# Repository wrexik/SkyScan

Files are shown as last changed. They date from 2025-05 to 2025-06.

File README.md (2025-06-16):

# SkyScan
An autopilot 4'' FPV drone with INAV and OpenIPC used for photogrametry!

---

**Say hello to SkyScan!** This is my personal project for [Hackclub Highway](https://highway.hackclub.com/). It will be used to take pictures and videos later to be used for photogrammetry and 3DGS.

 -> Just like this: [3DGS example](https://splatter.app/s/c07-ax0)

## Table of Ideas
- Under 250g
- 4" frame
- Digital FPV with OpenIPC
- INAV - GPS and Mission planning
- 4S battery

## Conectivity
- OpenIPC - 2.4GHz > Realtime HD video
- ELRS - 900MHz > Long range control
- GPS - 1.5GHz > Location & telemetry

## Why did I make this?
As a someone who got absolutlely obsessed with photogrammetry and 3DGS, I wanted to not be limited to taking photos from the bottom of the object or building.
I was told that I just need to get a drone, you know. Get. A. Drone. Then highway email came to me, and I was like, "I can make my own drone, and it will be better than anything you can buy!". OFC! So this is my journey how I learned about all the components, learned how to CAD and how to stay motivated for a longer period of time.

## What is this?
The idea is to create a lightweight drone, that you can just say a location and it will take photos of the object from all angles, and then you can use those photos to create a 3D model of the object.
Like something that DJI has, but with no hardware limitations and open source software!

## Custom 3D Printed Frame
Ive designed a custom frame that could be printed on all 22x22cm printers. So that you could easily replicate it. The frame is designed to be lightweight, but also strong enough to withstand crashes. It supports both 25.5x25.5mm and 30.5x30.5mm mounting patterns for the AIO flight controller and VTX. The files are fully open source and available in the [3d project files](/3d%20parts/3d%20project%20files/) folder.  **Customize it as you want!**
You can print it in any material you want. Or even use CNC machine.

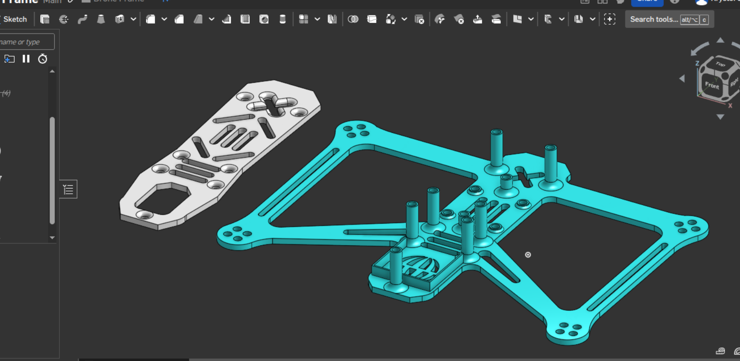
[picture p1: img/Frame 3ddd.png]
Frame

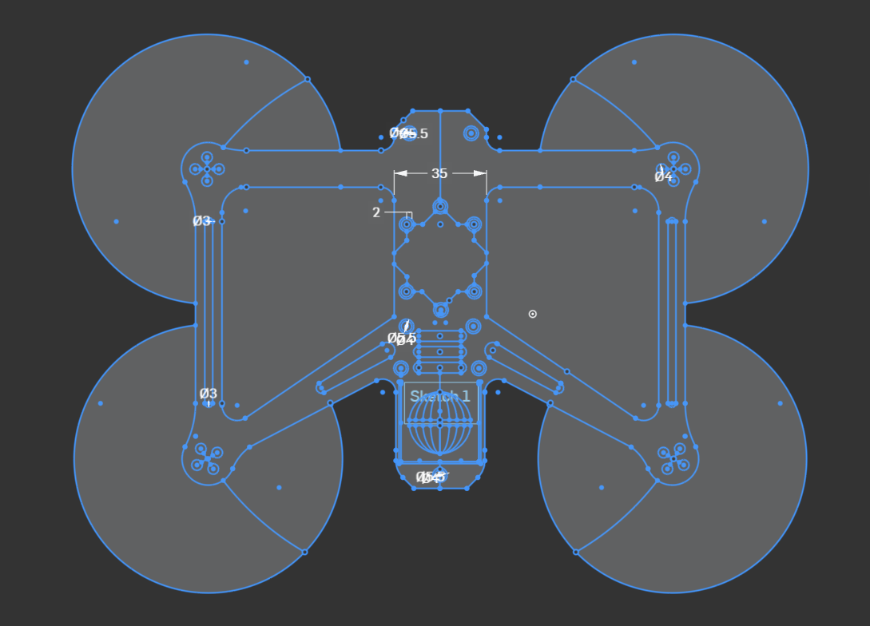
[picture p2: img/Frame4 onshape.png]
Frame drawing

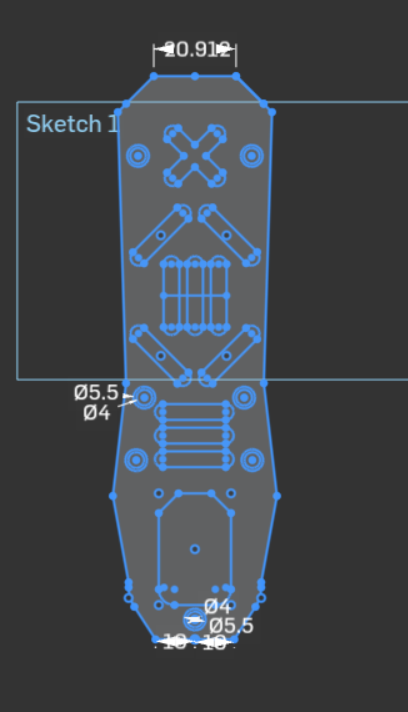
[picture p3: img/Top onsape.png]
Frame shell


``note that the frame does not currently have a camara mount, waiting for the grant to be approved to buy a camera and make it``

# Hardware

  | **Component**                     | **Model / Specs**                                                       | **Notes**                         |
|----------------------------------|--------------------------------------------------------------------------|-----------------------------------|
| **Frame**                        |  Custom 3d printed, my design                                               | supports 25.5x25.5mm, 30.5x30.5mm |
| **Flight Controller + ESC**      | Speedybee F405 AIO 40A (25.5x25.5mm)                                     | BLHeli_32, Bluejay, 3–6S support  |
| **Motors**                       | 4x T-Motor P1604 3800KV                                                  | 4S optimized, 9x9mm mount         |
| **Receiver**                     | Radiomaster XR1 Nano Dual-Band ELRS 2.4GHz + 900MHz                      | High range redundancy             |
| **Radio Controller**             | Radiomaster Pocket (TC-style with built-in ELRS 2.4GHz)                  | No external module required       |
| **Camera & VTX**                 | EMAX Wyvern Link Alpha (OpenIPC support, 5.8GHz HD, 100mW)               | OpenIPC-compatible                |
| **Props**                        | Gemfan Hurricane 4023 / HQProp T4x2.5x3                                  | For 4" efficiency/freestyle       |
| **Battery (light)**              | 4S 850mAh Li-ion                                                         | Sub-250g compatible               |
| **Battery (long range)**         | 4S 18650 3000mAh Li-ion (e.g., VTC6 pack)                                | Up to 40+ min flight              |

This is the camera that makes this all possible. It is a 5.8GHz digital FPV camera with OpenIPC support, which allows you to stream HD video in real-time.
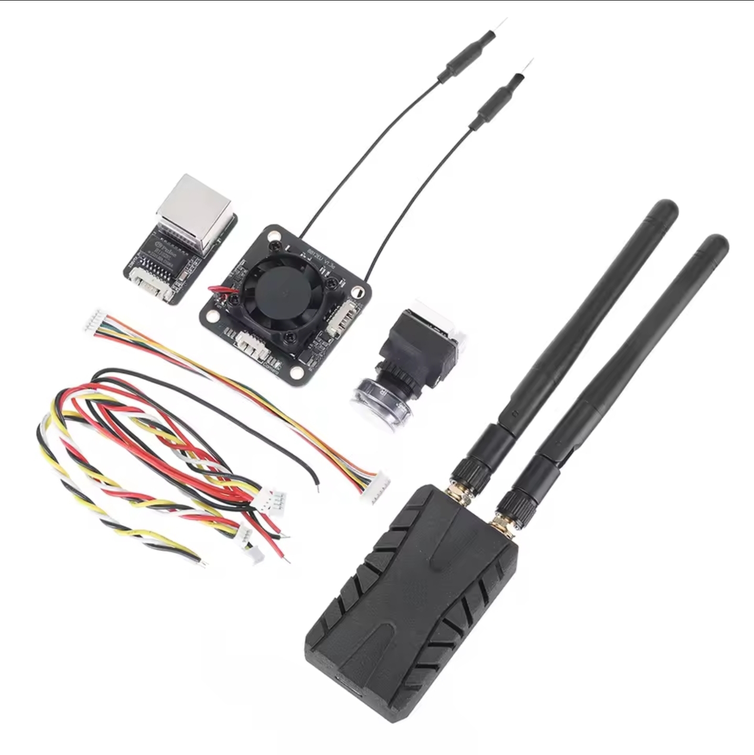
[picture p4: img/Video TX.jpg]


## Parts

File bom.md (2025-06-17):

| **Component** | **Model / Specs** | **Notes** | **Price (CZK)** | **Price (USD)** | **Link** |
|---|---|---|---|---|---|
| Frame | Custom 3d printed, my design (Cost is material spool petg-cf) | supports 25.5x25.5mm, 30.5x30.5mm | 500 | 24 | |
| Flight Controller + ESC | Speedybee F405 AIO 40A (25.5x25.5mm) | BLHeli_32, Bluejay, 3–6S support | 1330 | 61 | [AliExpress](https://a.aliexpress.com/_Ez89AS2) |
| Motors | 4x T-Motor P1604 3800KV | 4S optimized, 9x9mm mount | 1142 | 52 | [AliExpress](https://a.aliexpress.com/_EINYVGa) |
| Receiver | Radiomaster XR1 Nano Dual-Band ELRS 2.4GHz + 900MHz | High range redundancy | 335 | 15 | [AliExpress](https://a.aliexpress.com/_ExRInKe) |
| Camera & VTX | EMAX Wyvern Link Alpha (OpenIPC support, 5.8GHz HD, 100mW) | OpenIPC-compatible | 2350 | 107 | [AliExpress](https://a.aliexpress.com/_EHbSKhC) |
| Props | Gemfan Hurricane 4023 / HQProp T4x2.5x3 | For 4" efficiency/freestyle | 130 | 6 | [AliExpress](https://a.aliexpress.com/_EzHnXNG) |
| Battery (light) | CNHL 4S 850mAh XT30 2pcs | Sub-250g compatible | 820 | 38 | [AliExpress](https://www.aliexpress.com/item/32848174970.html) |
| GPS | Generic M8Q or BN-220 GPS Module | For navigation and failsafe | 600 | 27 | [AliExpress](https://a.aliexpress.com/_ExEMGLG) |
| Buzzer | Standard 5V buzzer with beacon function | Optional but useful | 45 | 2 | [AliExpress](https://a.aliexpress.com/_EHUrHM6) |
| VTX Antenna | U.FL 5.8GHz Antenna | Compatible with Wyvern VTX | 300 | 14 | [AliExpress](https://a.aliexpress.com/_Ev1Kqw6) |
| **Total** | | | **7282** | **329.15** | |

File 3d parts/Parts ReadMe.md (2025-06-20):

The Final 3D parts are:

[Top Shell](/3d%20parts/Top%20Shell.stl)

[Bottom Frame](/3d%20parts/Bottom%20Frame.stl)

The DWG is located in the *3d project files* folder.

And here is the link for OnShape: [Link](https://cad.onshape.com/documents/29a5ea5b7ab0b002b2ab2d66/w/dfc60f1223006b31794c7fb2/e/e7f5c2a8a30eddbf3b560972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)

Some basic measurements
- All Holes are 1.5mm
- 30.5 x 30.5mm and 25.5 x 25.5 mounting frames
- Space for 19 x 19mm GPS module in the back
- Properels are 102.1mm (4 inch)

| Component | Mounting | Diameter | Notes |
| --- | --- | ----- | --- |
| FC AIO | 25.5 x 25.5mm | 1.5mm | 4 x holes |
| VTX | 30.5 x 30.5mm | unknown | 4 x holes|
| Camera | 2 screws from the sides | n/a | 2 x holes, 19 x 19mm body |
| Motors | 9 x 9 mm | M2 / 1.5mm | 4 x holes |

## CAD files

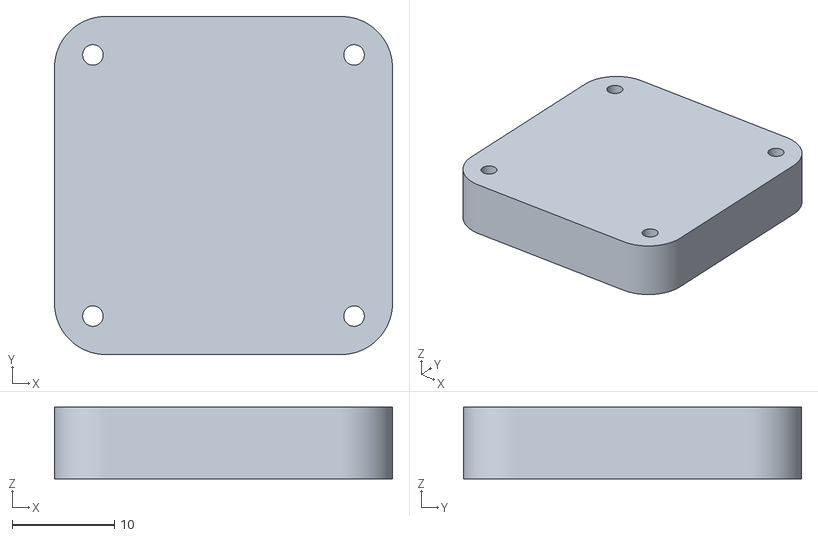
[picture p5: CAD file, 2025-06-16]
3d parts/FC Model.stl
33.0 x 33.0 x 7.00

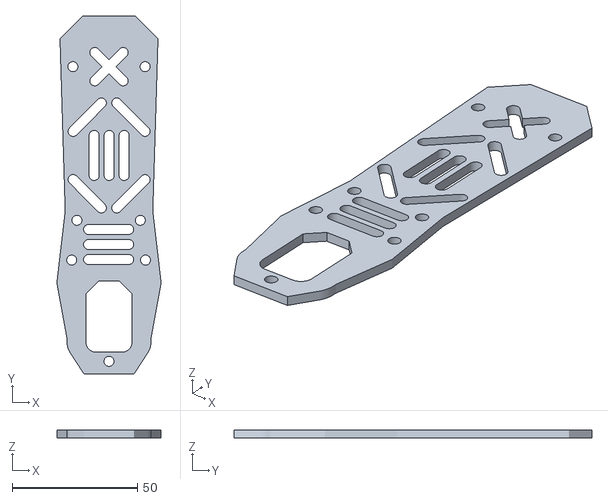
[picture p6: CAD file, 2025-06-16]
3d parts/Top Shell Sharp.stl
41.7 x 143.1 x 3.00

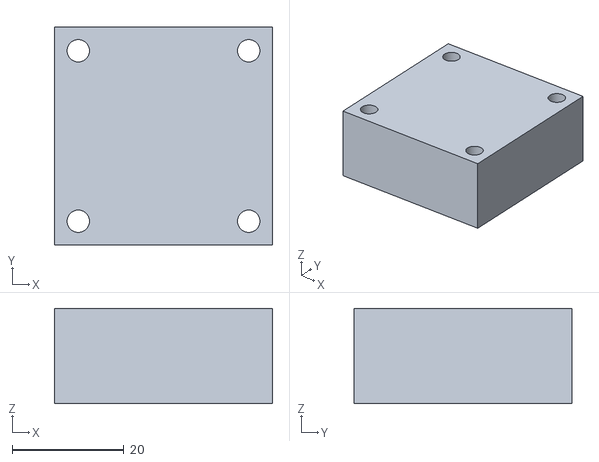
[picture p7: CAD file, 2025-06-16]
3d parts/VTX with fan model.stl
39.0 x 39.0 x 17.0

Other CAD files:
3d parts/3d project files/Drone DWG.dwg

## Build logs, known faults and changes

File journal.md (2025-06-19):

---
title: "SkyScan"
author: "Wrexik"
description: "An autopilot 4'' FPV drone with INAV and OpenIPC used for photogrammetry!"
created_at: "2025-05-21"
time_spent: "6-7h"
---

# 05-21: Initial Repository Creation & Ideas
``Aprox. 2,5 hours of research``

Created a new repository for the SkyScan project.  
I've watched videos on drone building and the INAV firmware.
- Looked into ELRS and OpenIPC for long-range control and video streaming.

Wrote down the following features I would like to accomplish:
- Under 250g due to regulations
- 4" frame
- Digital FPV with OpenIPC
- 4S battery
- GPS and Mission planning with INAV

- Looked into compatibility of OpenIPC and ELRS frequencies. Both are 2.4GHz. So I will need to use a 900MHz ELRS module to make sure that the 2.4GHz and 900MHz modules are not **interfering with each other**.
- Looked up options for the OpenIPC system. Decided to go with **Wyvern Link (Alpha) OpenIPC - 100mW VTX** for its price and good camera.

Aliexpress will be the shop I will be sourcing from — cheap shipping and a huge selection of parts. I have only good experience with Aliexpress. So there isn't another option.

Okay, a few hours later and I have actually a better option for the camera. I will be using the **Eachine Sphere Link 5.8GHz WIFI Digital HD**. Since the Wyvern Link does not support onboard recording, this will be a much better option. And I will be able to use the **5.8GHz** frequency for the video and 2.4GHz for the ELRS.

> this is the Eachine Sphere VTX  
Eachine Sphere VTX

- This was about 2.5 hours of research. I will be continuing to look into the components and their compatibility.

# 05-21: Frame, FC, Motors

I prioritized selecting the camera first because that's the main part of the drone for the actual 3D scanning.

I've continued to look up parts and I think I have a quite good combination now. I'm especially happy with the frame. It's built so the props don’t show in the camera feed. **Clear video is important!**

### As of now, I have selected the following components:

| Component | Details / Notes |
| --- | --- |
| **Frame** | **JMT LR4 169mm (4")** — supports 20x20 / 25.5x25.5mm stacks |
| **Flight Controller + ESC** | **SpeedyBee F405 AIO 40A** — powerful, 25.5x25.5mm mount (fits with adapter or printed plate) |
| **Motors** | **T-Motor P1604 3800KV** — perfect for 4S & 4" props; great efficiency for cruising |
| **Camera/VTX** | **Eachine Sphere Link** — 1080p onboard DVR, MAVLink, 800mW digital FPV |
| **Receiver** | **Radiomaster XR1 Nano ELRS** 2.4GHz/900MHz dual-band — fully INAV + ELRS compatible |

> The frame I've chosen to go with  
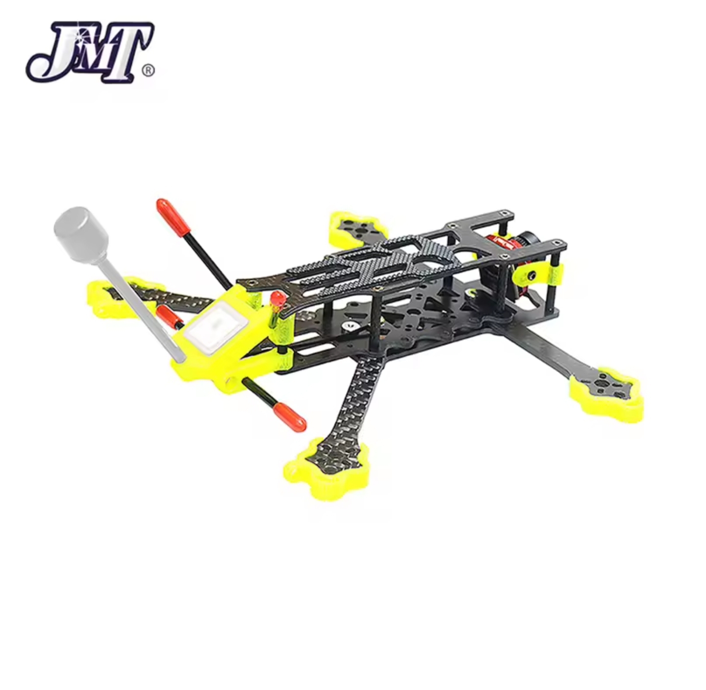
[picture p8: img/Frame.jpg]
Drone Frame


Next steps:
- Look into the GPS recommended by the frame manufacturer, since it already has a GPS mount.
- Learn more about props and their compatibility with the motors.
- Finish with battery selection. **And establish a weight budget.**

My plan for the custom parts are legs that I will model and 3D print. I will also be using a 3D printed mount for the camera. As for custom hardware, the FC has an I2C port; I could use that for a LIDAR or RGB.

That's all for now. Will be back soon!

# 05-22: Component Selection & Weight Budget

`2 hours to school well spent :P`

Hey again, today I started working right after I got into my train. I've decided on a GPS module that will be needed for the drone to have a good position hold while taking pictures.  
The GPS should also have a magnetometer so the drone knows its direction — which the **Beitian BN-880 BN880** has.

Last night I watched a few videos and all of the featured drones had a buzzer. So I figured I might also add one, the FC supports it.

| Component  | Details / Notes |
| --- | --- |
| **GPS** | **Beitian BN-880 BN880 Flight Controller GPS** — Fast and accurate, has magnetometer |
| **Buzzer** | **Pixhawk PX4 Buzzer** — really compact |
| **Props**  | **Gemfan 4023 1.5mm 2mm 4inch 3 blade** — Good looking and in the right size. They should be made for the brand of our motors |

Now I'm looking into props. They should have a 1.5mm hole and 3 blades — 4 inch size of course.  
From what I understand the **4023** are suitable. I've chosen a **pack of 16** since they are quite fragile.

I really like this process of looking up parts and matching them with each other. It’s like building computers — but it FLIES!

With the props added it looks quite complete, just checking a few things with the seller of the drone frame so I could be sure with the dimensions. I CANT WAIT!

I will be sourcing my own batteries & controller. The software part is also what I’m looking forward to — I found some that I could modify for my 3D scanning implementation!

I will have my friend run over the parts and check some of the fitment. The VTX will have to have a custom 3D printed adapter because it’s 0.5mm off. That's no problem — I will practice my patience and CAD skills.

Also an interesting thing I found while researching RX modules and interfering frequencies — the current **Radiomaster XR1 Nano ELRS** is dual-band. So it supports both 2.4GHz and 900MHz. That means I could upgrade for longer range down the road!

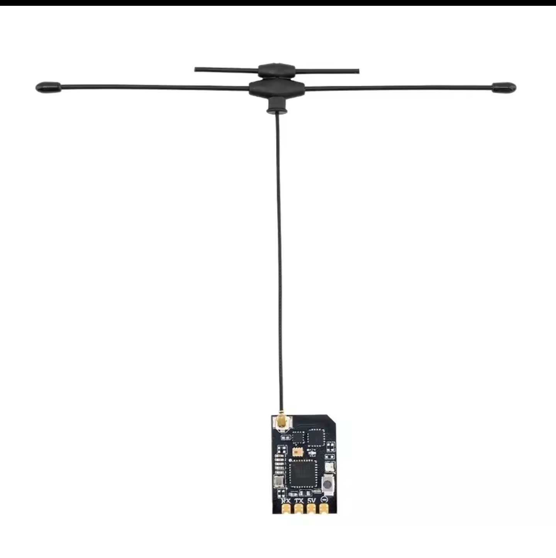
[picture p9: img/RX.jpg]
ELRS RX


Hey I'm back, 2 classes later, I've found this cute pair of lollipop antennas. They will be great for the VTX. Since the drone will be operated remotely on a monitor I would really like a good video feed. Might implement computer vision for object detection.

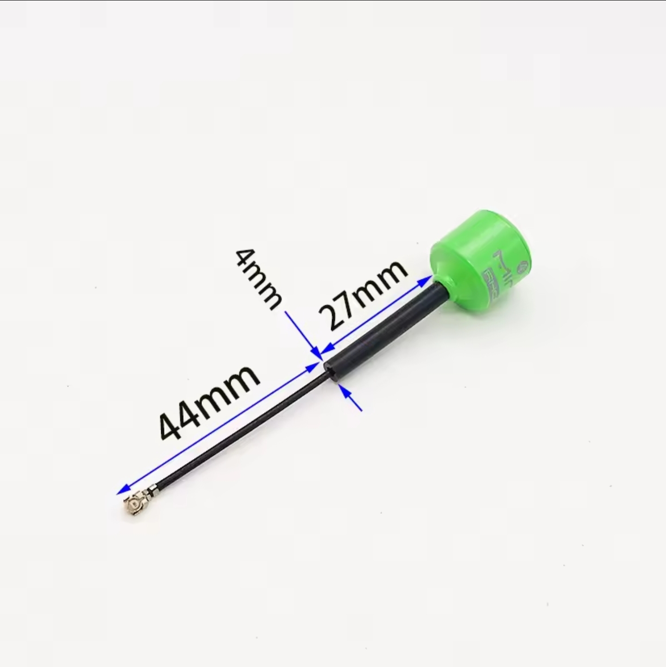
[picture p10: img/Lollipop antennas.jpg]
Antennas


# 05-22/23: Final costs

`took more or less about 30 minutes`

| Parts | Link |  Costs  + Shipping  |
| --- | --- | :---: |
| Frame | https://a.aliexpress.com/_EvwVZDU | 730 CZK - 33.15 USD |
| VTX | https://a.aliexpress.com/_EHbSKhC | 2350 CZK - 107 USD  |
| Motors | https://a.aliexpress.com/_EINYVGa | 1142 CZK - 52 USD |
| VTX Antenna | https://a.aliexpress.com/_Ev1Kqw6 |  300 CZK - 14 USD |
| FC AIO | https://a.aliexpress.com/_Ez89AS2 | 1330 CZK - 61 USD |
| Buzzer | https://a.aliexpress.com/_EHUrHM6 | 45 CZK - 2 USD |
| Props | https://a.aliexpress.com/_EzHnXNG |  130 CZK - 6 USD |
| GPS | https://a.aliexpress.com/_ExEMGLG |  600 CZK - 27 USD |
| RX | https://a.aliexpress.com/_ExRInKe |  335 CZK - 15 USD |
|TOTAL||317.15 USD|

The software side will be so much fun. Im looking forward to it.

---

# 06-11: Custom Frame Modeling for 3D Printing
`2 hours of 3D modeling`

Hey, it's Wrexik again!
Since highway is about making custom parts, so it would make sense to model the frame in 3D. To get the project **approved**! Today I will gather all the measurements and dimensions of the components for the build. I will also be looking for a good 3D material to print the frame with. So far I have been more towards PETG but ABS is also a good option. 
PETG with carbon fiber would be pretty cool. But I dont know if my printer is compatible with it. I will have to check that out.

Ok, now the measurements. I will check out the camera, VTX, FC, motors and GPS.
| Component | Mounting | Diameter | Notes |
| --- | --- | ----- | --- |
| FC AIO | 25.5 x 25.5mm | 2mm | 4 x holes |
| VTX | 30.5 x 30.5mm | unknown | 4 x holes|
| Camera | 2 screws from the sides | n/a | 2 x holes, 19 x 19mm body |
| Motors | 9 x 9 mm | M2 / 2mm | 4 x holes |

Next up, making some kind of footprint for the components. To better understand the way they will fit together.
Decided to try Onshape, ive been using Plasticity for a while but I want to try something new.

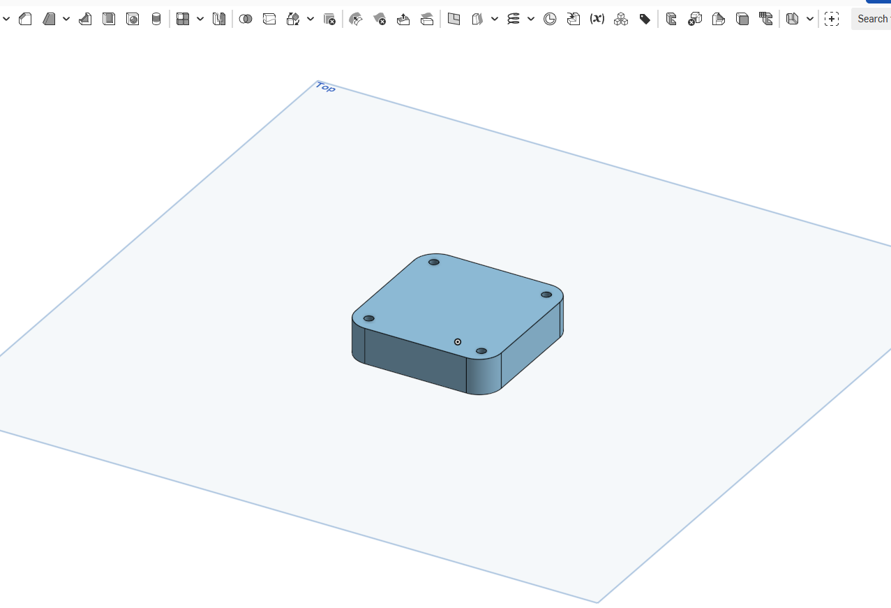
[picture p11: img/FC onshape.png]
Onshape FC model


Its really diferent. I have modeled the Motor and FC so far.
Now im going to model the VTC and GPS.
Here we go then... Did the GPS it will only serve as a reference for the mount. I might skip the GPS mount for now, since I will be using a 3D printed one anyway.
Onto the VTX, Echine doesnt have a good description of the dimensions, so again it will be only a refrence for the frame mounting.

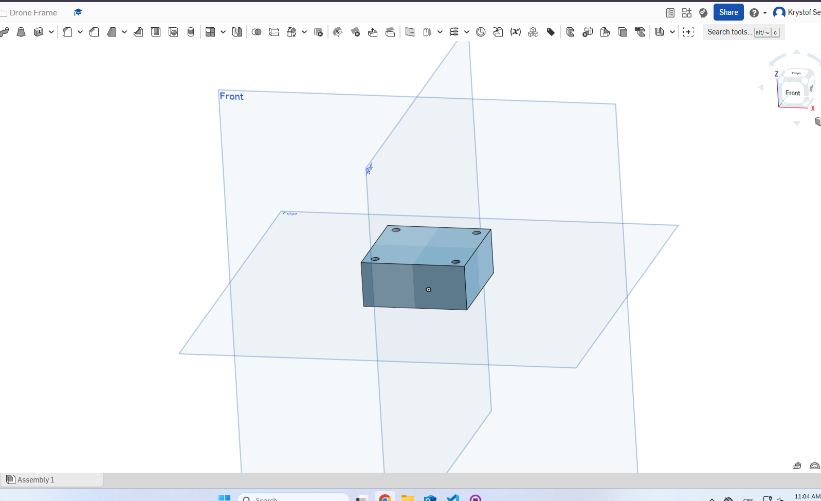
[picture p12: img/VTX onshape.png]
Onshape VTX model


They dont say if the hole is M2 or M3 so I did them as M2. I will have to check that out later. Or just add silicone feet to match the size.

Now the bigger part, the frame itself. I will choose the selected frame as a refrence, and modify it to my liking. It will be pretty basic, but I will be able to modifiy it later on and update it.
The plan is to have "Deadcat" shaped arms, for clean video without the props in the frame. And really lightweight. I have 10 minutes left of the current class, so I will get things togeter and see how it goes.

Anddd End. I've only managed to experiment with the frame. And get the initial idea.

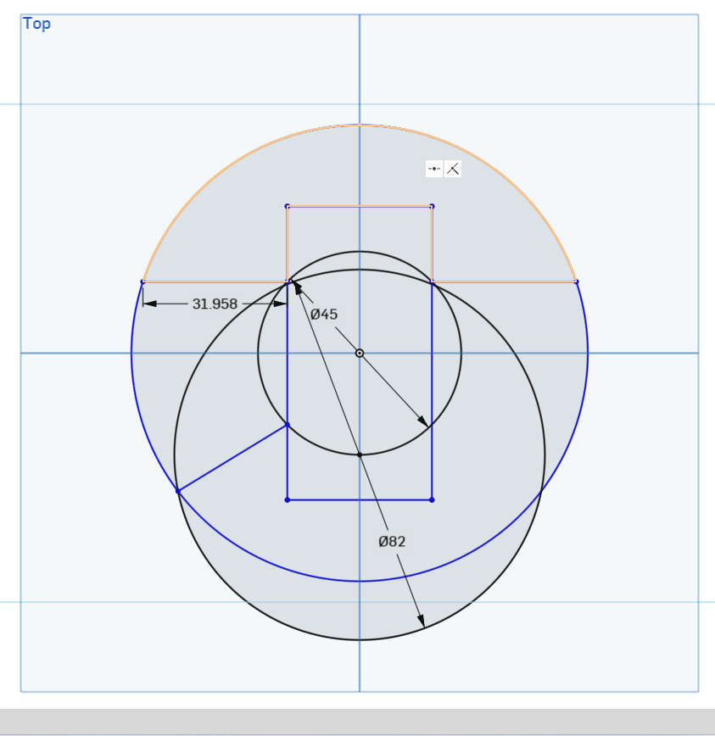
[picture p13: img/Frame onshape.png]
Onshape Frame model


# 06-12: More 3D Design & Frame Modeling
``1,5 hours of 3D modeling``

Ive added the propereller dimensions to make it easier to understand the layout. Ive also made the body little bit longer to fit everything in. It will also help with the center of gravity. I have to shower and go to bed, so I will continue tomorrow. But I think it looks super cool, with the rounded edges. *YEPEE*

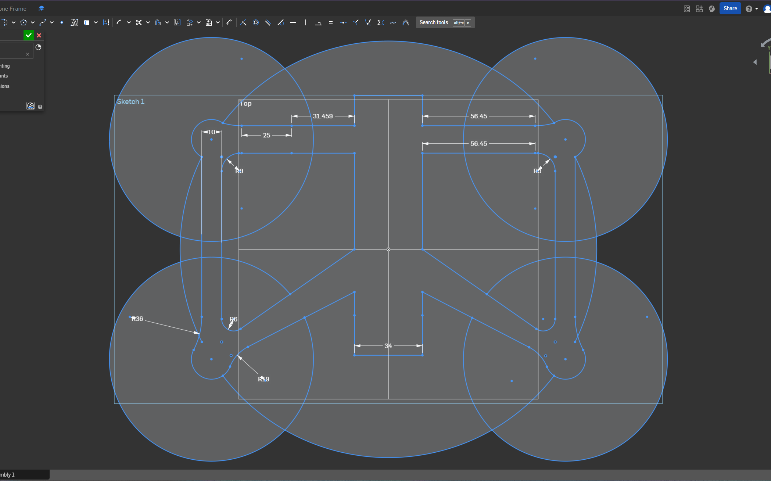
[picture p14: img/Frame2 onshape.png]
Onshape Frame model 2


tomorrow I will try to excrude the frame and try to print the very first prototype. Just to see the sizes and the fitment of the components. Im looking forward to it!

# 06-14: First Prototype Printed
Today I fixed some of the errors in the frame structure. The arms werent the same, I might use mirror mode next time. Ive also rounded more of the frame, it looks super cool now! When I came home from school I extruded the frame by 3mm and tryed to print it. It came in about 28g and 34m of print time. Just in PLA nothing fancy.
Next up, I will be adding the mounting holes and standofs. And the "roof" of the drone.

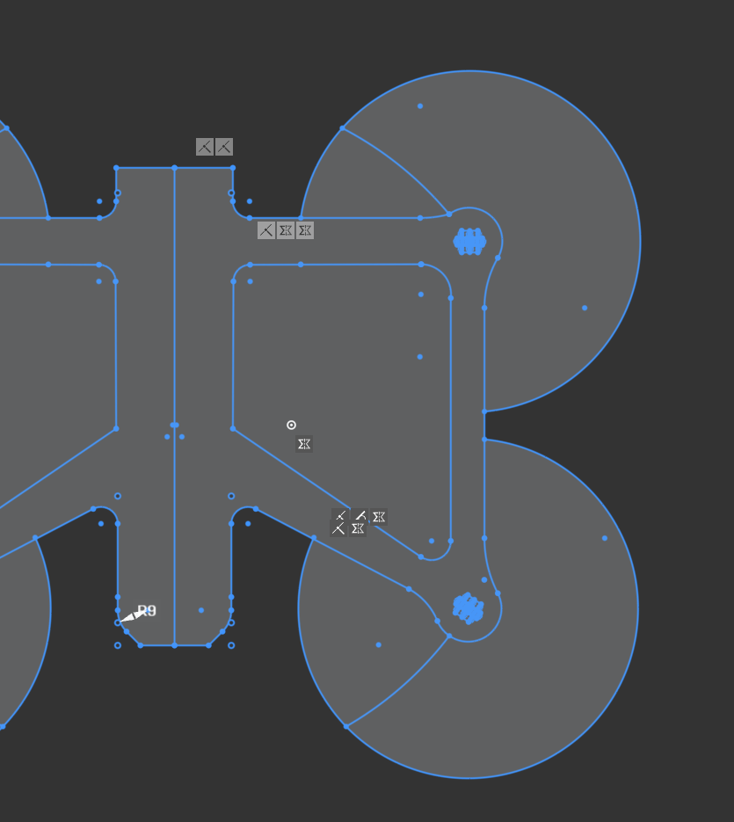
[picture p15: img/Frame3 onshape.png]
Onshape Frame model 3


Ive added the mounting holes for motors and made the back of the drone longer to easily fit the gps and stuff. I will be experementing with the mounting for the motors, Ive made them ajustable. But also left the M2 holes for the non ajustable version. The prototype is printed, older version but it looks sick!

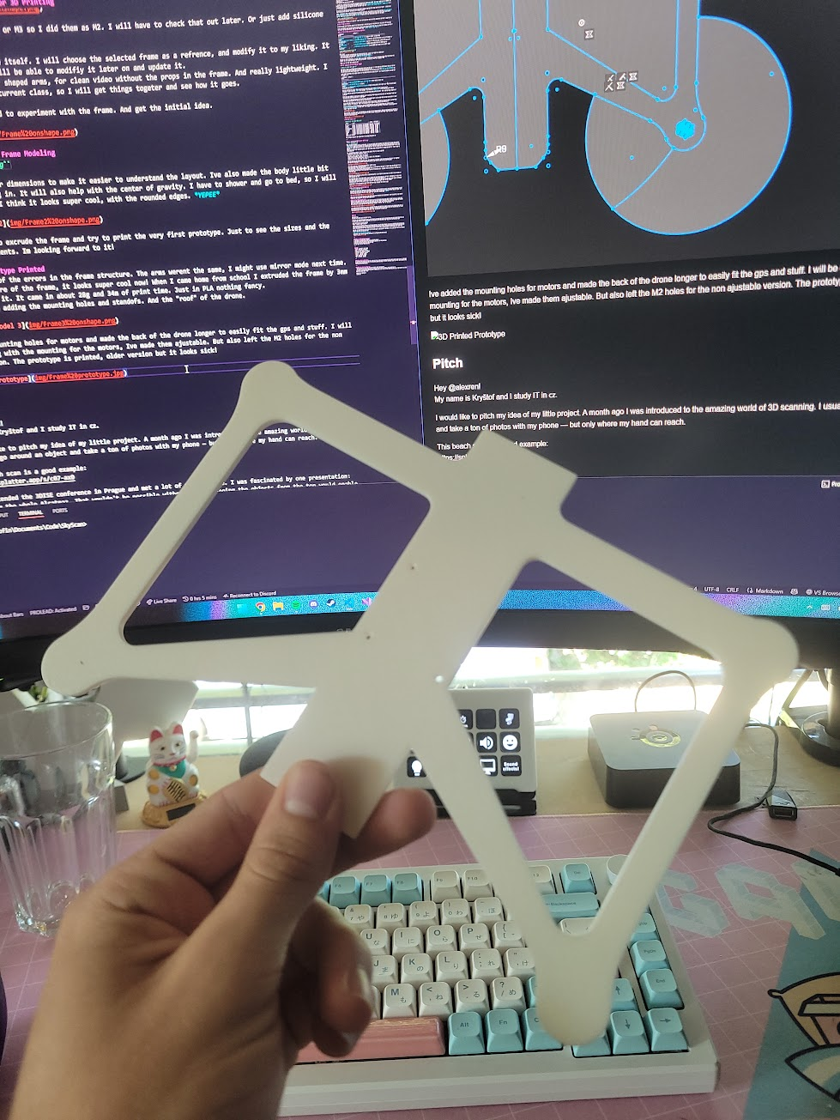
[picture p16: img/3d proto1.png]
3D Printed Prototype


Sorry fot the image quality, my S24 Ultra broke :/.

# 06-16 More CAD! Weight reduction.

``Took some time, 3,5 of CAD and stuff``

Hey, Ive been contimuing to model the frame. Ive looked up frame models and made it how I think it could work. I had the screw dimensions wrong, should be fixed now. I still dont know the diameter of the screw hole on the VTX. In case thats wrong it could be easily fixed after I get the parts from the grant. Ive added holes for mounting the roof of the drone. It will be pretty much the same thing like on the bottom, but with more holes and grill for the VTX fan. Well he might be covered by the battery, but it should work even without it. As far as my motivation goes, Im "motimaxxed" Im doing my best with the documentation for yall. I will work on the ReadMe next. With pretty screenshots. Really praying for approval rn.
Here is the current status of the drone. I had a while to work on it in class.

Onshape Frame model 4

I also looked up some filaments and compared PET-G CF with other options. And again again more holes! Starting with the top now, I need to figure out the camera mount. But there is also nearly to no documentation like with the VTX. Top will be mostly holes with a place to mount the strap for the battery. With im not sure also, what battery will I have to use. Some custom 18650 cells?? Also an option.

But I have no experience, cool to experiment with tho. Okay moving to the top...

Little while later I have this thing. I may ajust the holes a little more, for the battery but the dimensions I hope are correct. 

Onshape top

I found out that you can actually share a link, so here it is [Onshape model](https://cad.onshape.com/documents/29a5ea5b7ab0b002b2ab2d66/w/dfc60f1223006b31794c7fb2/e/e7f5c2a8a30eddbf3b560972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)
I turned off exporting since I want to be the one to post **my** model to Printables :D

And we are 3d!

We are 3D!

Ive also smoothed out the corners of the rods and some shapes to make it look smooth. 3D printing is better with way less material waste, over subtractive machining. The thing on the back is for the GPS. It isnt accurate but for now as proof of concept it will work really well. I hope this makes the project acceptable to fund me. I strugled but look what I learned! Amazing. Still Im looking forward programing it more tho :D. 

# 06-19: More 3D Design & Second Prototype Printed
``5 hours of 3D modeling and printing``

Ive printed the second prototype of the frame. The holes in the frame added a lot of rigidity to the frame. I was quite surprised how well and stable the back arms are. I will be adding more holes to the front arms, since they are quite thick. And still flexible. Ive printed it in PLA with 25% infill. The weight is was around 30g. 

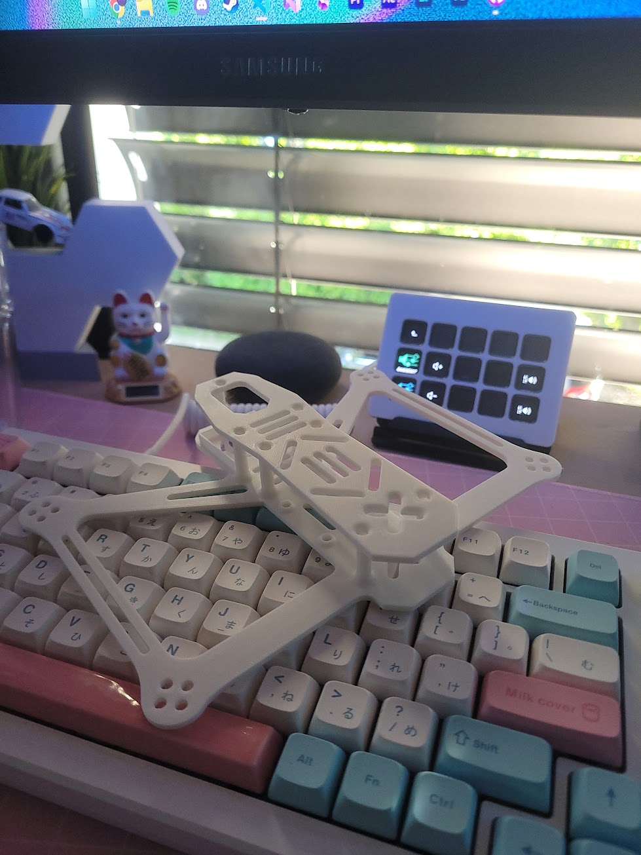
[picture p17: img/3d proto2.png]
3D Printed Prototype 2


There was my error with the hole sizes, I was trying to screw right into the plastic. M2 screws. But they are too big. Discussed with Tony that 1.5mm are more suitable. So I will be adjusting the model to fit the M2 screws. 

Since I had whole 4 lessons to work on the project, I went kinda crazy. I didnt take any screenshots of the process, but I have the final result. I have added more holes to make the vertical area bigger on the arm. This will help with the rigidity of the frame. 

Im also experimenting with extruded "rods" to make the frame more rigid. I will be adding them to the front arms, since they are quite thick. And still flexible.

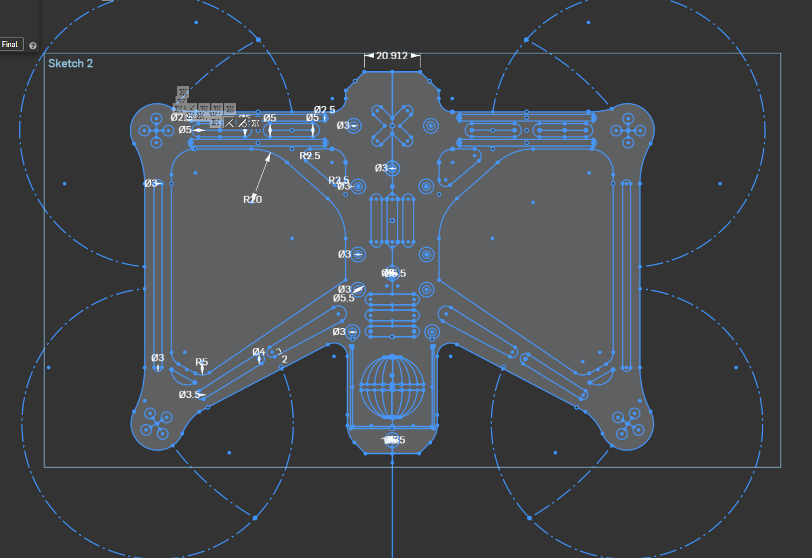
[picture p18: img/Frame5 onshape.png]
Onshape Frame model 5


Now Im going to extrude the whole frame with the changes. And smooth out the edges of some features. It will also add material to make it stronger. Well, here goes nothing. I will be printing it when I get home. I might try petg this time.

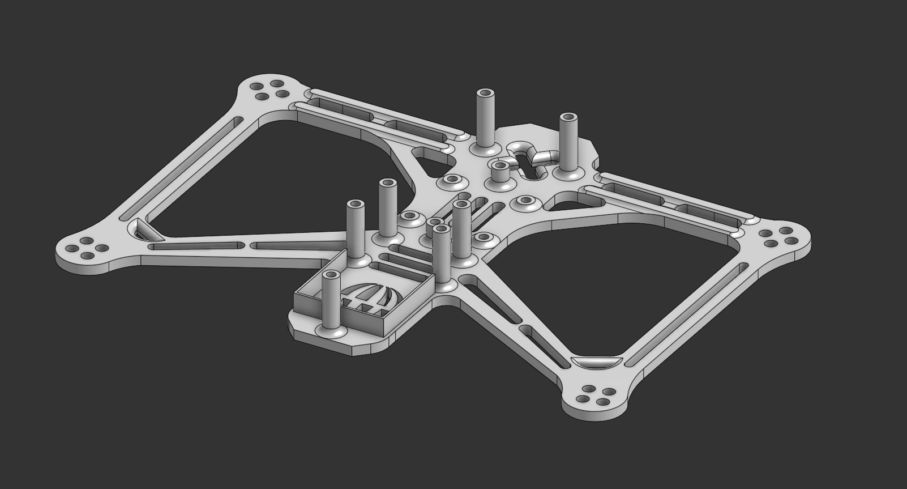
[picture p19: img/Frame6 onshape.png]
Onshape Frame model 6


Alright back home, Im writing on my laptop this time so I dont have to commit so offen. Lets slice the model and see how it goes. I predict that the print will take around 1 hour and 30 minutes. The weight should be around 40g. I will be using the same 25% of gyroid infill. I will be using the same settings as last time, with a 0.4mm nozzle.

And here it is! Its even more sturdy and rigid than the last one! The rods on the front arms are actually great and working as intended. I was surprised how well it got improved. Ive also made it a little bit taller, witch helped to compensate all the holes in the frame. So now both axis are strong.

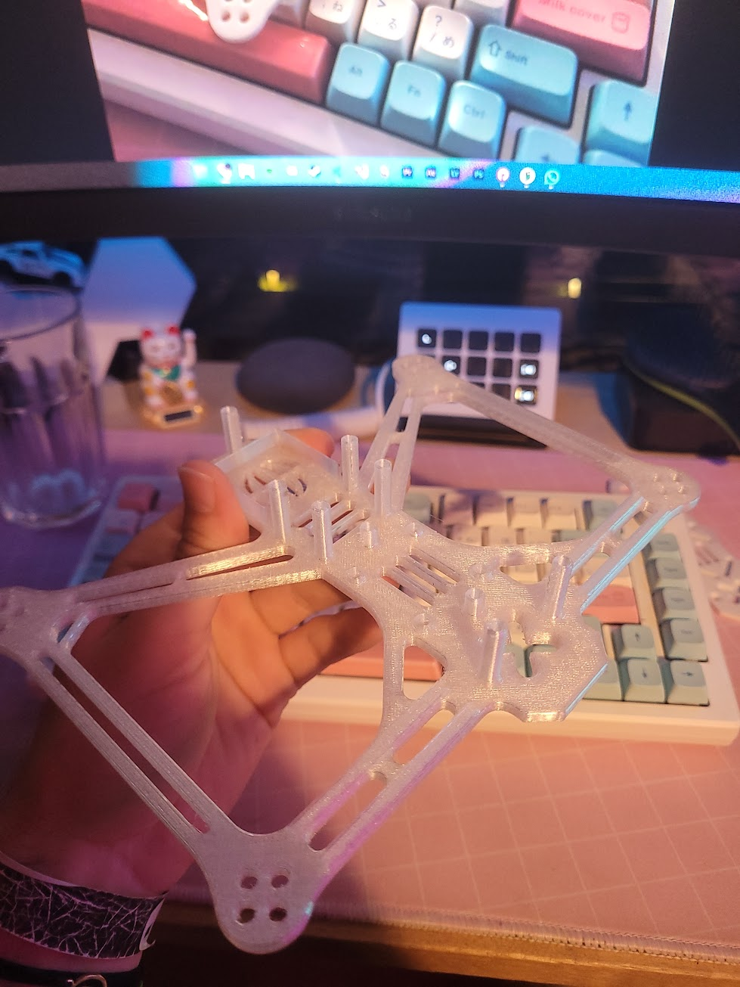
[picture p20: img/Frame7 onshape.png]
Onshape Frame model 7


I will talk to Alex, what does he think. I dont really see the point of making the frame any more complex. I would definitely try to work even more on the rigidity, but in this weigh class and size, wihout a payload, I think it is okay. 

See you tomorrow!

## Pitch

Hey @alexren!  
My name is Kryštof and I study IT in 🇨🇿.

I would like to pitch my idea of my little project. A month ago I was introduced to the amazing world of 3D scanning. I usually go around an object and take a ton of photos with my phone — but only where my hand can reach.

This beach scan is a good example:  
https://splatter.app/s/c07-ax0

I’ve attended the 3DISE conference in Prague and met a lot of smart people. I was fascinated by one presentation: scanning the whole Alcatraz. That wouldn't be possible without drones. Seeing the objects from the top would enable me to scan abandoned buildings and continue exploring the topic of photogrammetry and 3D gaussian splatting.

DJI has its own enterprise solution for 3D scanning — so why wouldn't we make it too, and open source it? Autonomous digitizing of buildings and sites.

**Examples of recent previous work:**  
SMD alarm clock, with 2 switches and buzzer to configure and wake you up:  
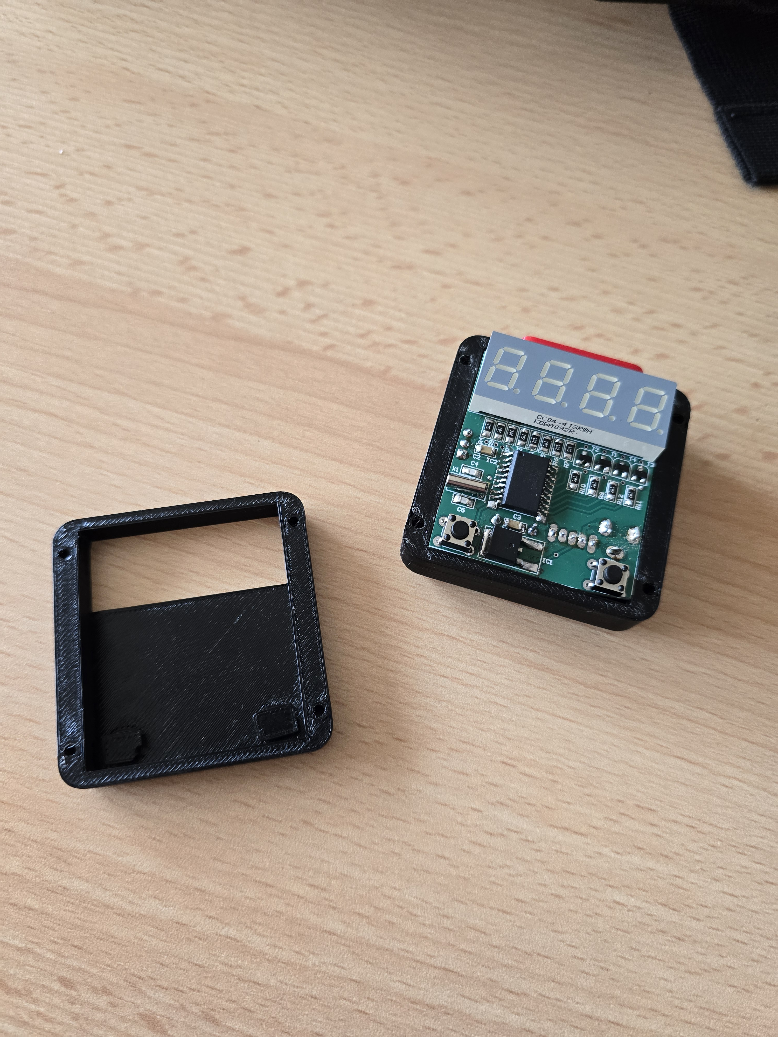
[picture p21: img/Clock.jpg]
SMD Clock


---

### What would be the build process:
1. Gather all the hardware needed.
2. 3D model a new mount for the camera and VTX adapter.
3. 3D print the rest of the frame with modification to fit the antennas.
4. Practice soldering & planning the steps.
5. Configure, Build, Code and Fly!

---

### BOM:
- Frame - 730 CZK / 33.15 USD
- VTX - 2350 CZK / 107 USD
- Motors - 1142 CZK / 52 USD
- VTX Antenna - 300 CZK / 14 USD
- FC AIO - 1330 CZK / 61 USD
- Buzzer - 45 CZK / 2 USD
- Props - 130 CZK / 6 USD
- GPS - 600 CZK / 27 USD
- RX - 335 CZK / 15 USD

---

### Why I know I can do this:
I wanted to build my own drone for a while. It is a fascinating hobby for me, and I want to get into it. And where else to start — just build one. I have pretty good knowledge in the IT software side, but this could open my heart to PCB designing and hardware.

---

### Why this deserves 10 points:
- It has quite a lot of new things for me to learn and explore.
- I think it is a unique idea, that could open this world for others like it did for me.
- I might not be making something super complex but I will be building something that was on my mind for a while. Super motivated about this.

Thanks for reading in,  
💕 Wrexik

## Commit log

2025-06-12 frame beta!
2025-06-17 added links
    [bom.csv]
2025-06-17 converted to .md
    added material cost, better formating
    [bom.csv]
2025-06-22 V2 Frame added
